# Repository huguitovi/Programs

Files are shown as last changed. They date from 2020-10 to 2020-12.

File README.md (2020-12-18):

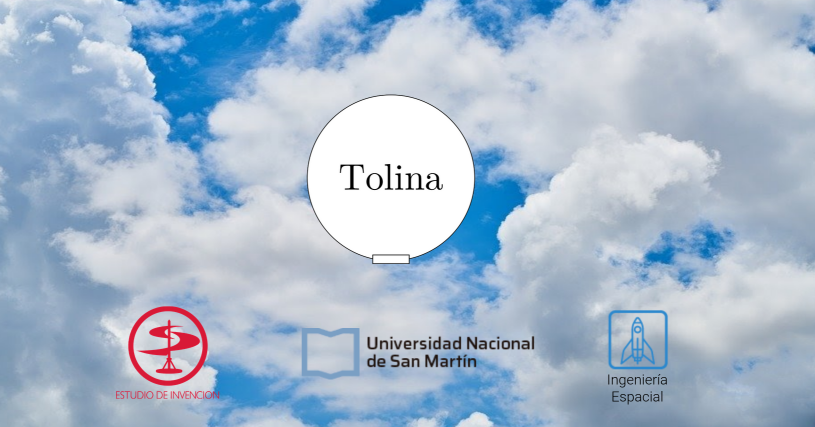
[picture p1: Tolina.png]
GitHub Logo


## Sobre Tolina

Tolina es un dirigible esférico, proyecto perteneciente a los estudiantes del segundo cuatrimestre de 2020 de la materia Proyecto Integrador II, de la carrera de [Ingenieria Espacial](http://www.unsam.edu.ar/ingenierias/#ingenierias) perteneciente a
la [Escuela de Ciencia y Tecnología](http://www.unsam.edu.ar/escuelas/ciencia/) de la [UNSAM](https://www.unsam.edu.ar/).

## Ingeniería Espacial
Argentina es uno de los siete países que tienen satélites propios. Los proyectos para aumentar la soberanía espacial demandan ingenieros con esta formación. Podrás diseñar vehículos y dispositivos cuyo ambiente está en el espacio, donde hay vacío, radiaciones electromagnéticas, temperaturas bajo cero y meteoritos. Esta es la primera carrera de América Latina en su tipo y tiene una orientación en sistemas complejos. La creatividad, la inventiva y la innovación son las habilidades esenciales de cualquier ingeniero. La Ingeniería Espacial implementará una nueva pedagogía para concebir, diseñar, implementar y operar sistemas, productos y servicios espaciales. Los alumnos participarán de proyectos integradores y multidisciplinarios dentro de un [Estudio de Invención](http://estudiodeinvencion.com.ar), que contará con un laboratorio de prototipado rápido y amplios espacios de trabajo con todas las herramientas y técnicas digitales modernas.

## Audiencia. ¿Para quién está pensado?
Tolina es realizado en medio de una crisis de salud mundial generada por la Pandemia de COVI-19, de tal forma es pensado como un medio para permitir a sus usarios una forma alternativa, de largo alcance de radiofrecuencia, larga vida de las baterias, para gestionar la logistica prioritaria de las vacunas a sectores de dificil acceso, tanto como de distintas mercancias, salvaguardando la salud y manteniendo la distncia social, recomendada por la [OMS](https://www.aaoms.org/practice-resources/covid-19-updates).

## Contenido
El objetivo de este repositorio es permitir al equipo trabajar desde sus casas, mantener al día los cambios de versión, abrir el trabajo a la comunidad y de esta forma gestionar más eficientemente el tiempo de desarrollo y ensayos de los distintos subsistemas.

## Requerimientos
Para utilizar estos códigos es necesario tener un PCDuino4 nano, el kit de desarrollo LoRaWAN ofrecido por Elemon SAMR34, clon de [Penguino Feather SAMR34](https://makertronika.com/penguino-samr34/) y demas componentes detallados en el [BOM](https://docs.google.com/spreadsheets/d/1q8VCjkfIKXkzYkmn2R5FzP_4t8kTszAMtYl-jQM-gV4/edit?usp=sharing). Los requermientos de sistema se detallan [aquí](https://github.com/huguitovi/Tolina/blob/master/documentos/Requerimientos.md).

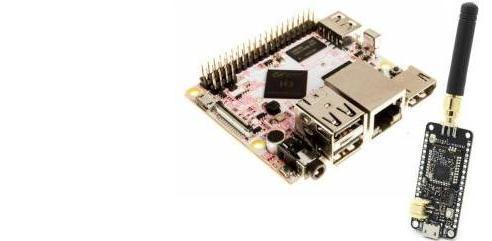
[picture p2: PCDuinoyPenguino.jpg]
image info


## Dedicación y duración
Este proyecto dura un cuatrimestre y es de dedicación completa por parte del equipo de estudiantes que en este tiempo deben tener listo y operativo el dirigible.

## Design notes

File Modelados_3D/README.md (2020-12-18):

# Modelados 3D

Tanto como para la determinación del centro de masa, como para facilitar aspectos relacionados a la integración realizada a distancia y en forma descentralizada, se realizaron los siguientes modelados 3D:

## PCDuino4 nano

Fabricante: [LinkSprite](https://www.linksprite.com/pcduino4-nano/)
Modelado: [OnShape](https://cad.onshape.com/documents/b4b0b3f34a575819a2707872/w/88d6b2fa41ddc3f8a9d6b3d2/e/b33581a21ca1b7f09e8596de)

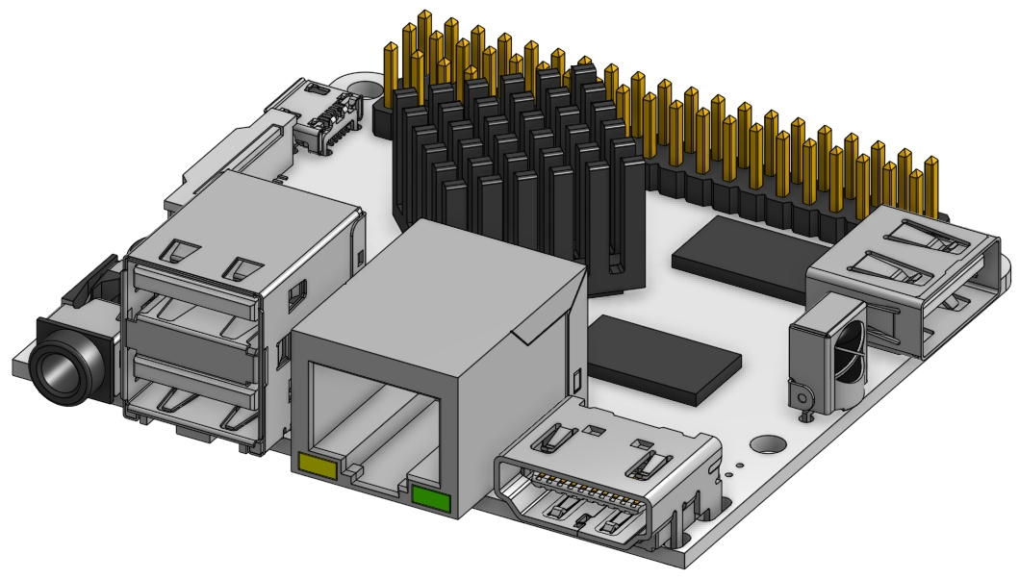
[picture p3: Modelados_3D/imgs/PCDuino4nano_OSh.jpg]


## EESAM34R

Fabricante: [Elemon](https://www.elemon.com.ar/Cotizar.aspx)
Modelado: [OnShape](https://cad.onshape.com/documents/ec4b6312847b79863e13bf8e/w/0436242ac0876fc591eb0102/e/217696dc8bc2e912b344ecc6)

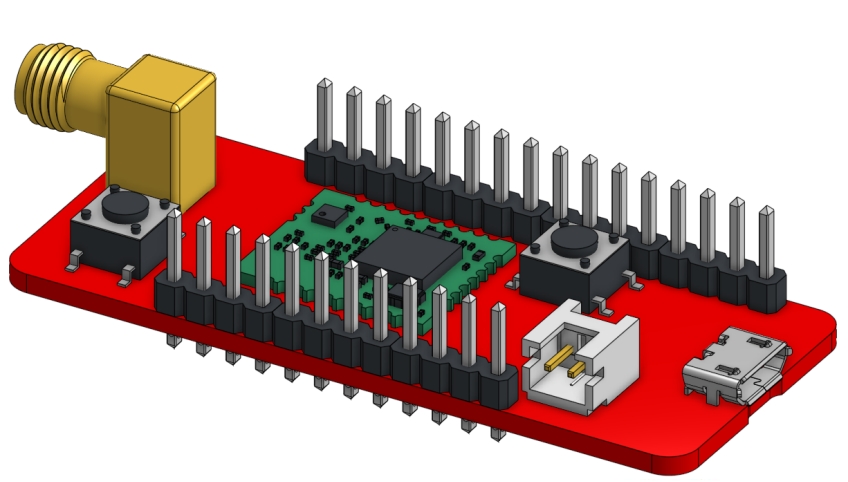
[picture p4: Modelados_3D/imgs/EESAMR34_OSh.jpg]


## Antena SGSM008-SMA/M-R/A-5

Fabricante: [Elemon](https://www.elemon.com.ar/Cotizar.aspx)
Modelado: [OnShape](https://cad.onshape.com/documents/461af691bdc8e8293b6acc81/w/5bf0a661077147eb908c0616/e/5cb2624135b9eea222923b98)

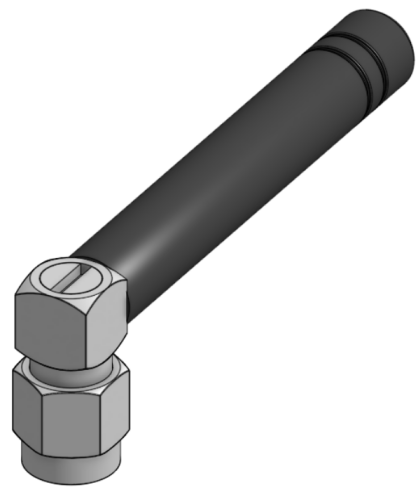
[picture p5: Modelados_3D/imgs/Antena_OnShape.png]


## PCB dedicado (Modulo controlador de 8 motores nativo de Tolina)

Fabricante: [Tolina](https://github.com/huguitovi/Tolina)
Modelado: [OnShape](https://cad.onshape.com/documents/81b609bb43d320c6a6baf298/w/e704fe0701eedfa0513e0479/e/23b6f936ed0f58f585dd623b)

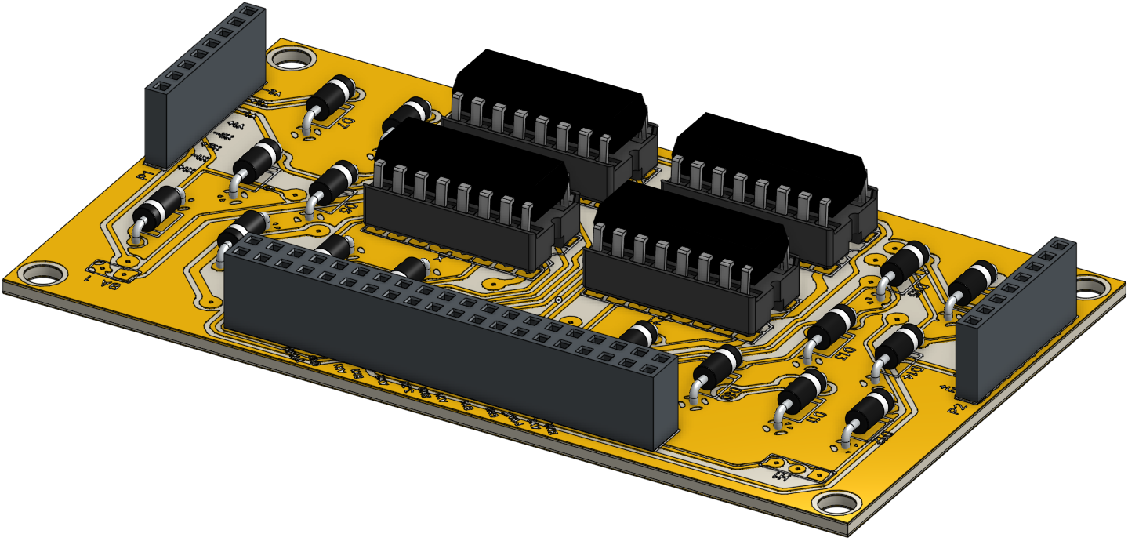
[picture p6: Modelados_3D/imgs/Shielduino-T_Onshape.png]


## Logitech C200 WebCam desarmada

Fabricante: [Logitech](https://support.logi.com/hc/en-us/articles/360023307014-Logitech-Webcam-C200-Technical-Specifications)
Modelado: [OnShape](https://cad.onshape.com/documents/c44ed40a48549f56abfa6e95/w/bb11458fc9d157a45261392b/e/d3aeba1b3881ed7b99e6e940)

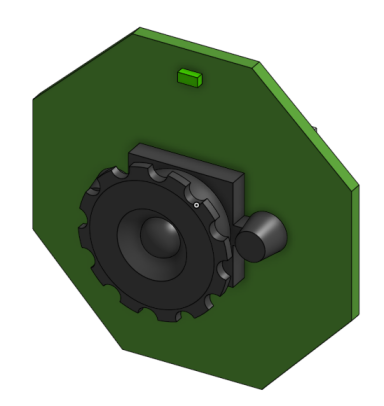
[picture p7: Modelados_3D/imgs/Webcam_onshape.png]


## SRF04

Modelado: [OnShape](https://cad.onshape.com/documents/197cf291449f2230b7baf36f/w/e24e00b610793ed7f297869d/e/b949f0ee36fcf4b4ce4800be)

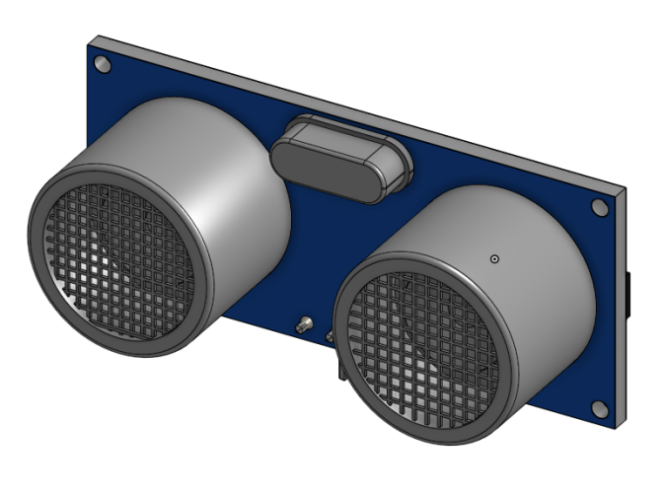
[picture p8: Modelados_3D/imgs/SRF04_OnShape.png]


## MPU9250 BMP260

Fabricante: [Bosch](https://www.bosch.com/)
Modelado: [OnShape](https://cad.onshape.com/documents/137634499555791615642d57/w/9201c79dbb14d58388e90772/e/1ceaf7b055e3bd4cd616bf7e)

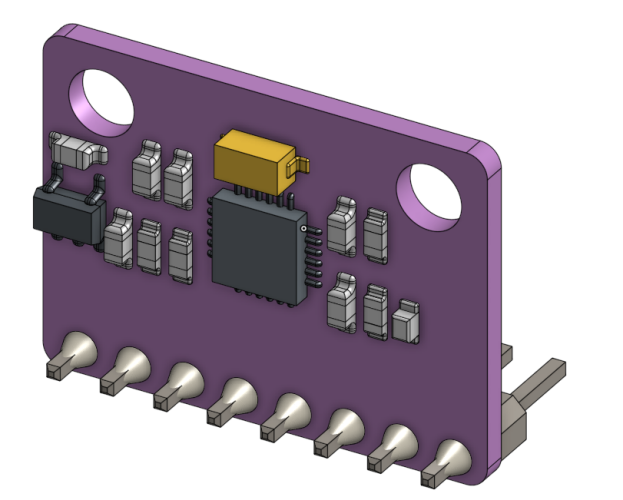
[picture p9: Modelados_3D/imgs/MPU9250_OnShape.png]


## JSN-SR04T

Fabricante: [JSN](https://www.elemon.com.ar/Cotizar.aspx)
Modelado: [OnShape](https://cad.onshape.com/documents/5689bac8cee0096f19e13d54/w/39e027f5c27cfc006658e57e/e/44e5082090eb61c592169ccd)

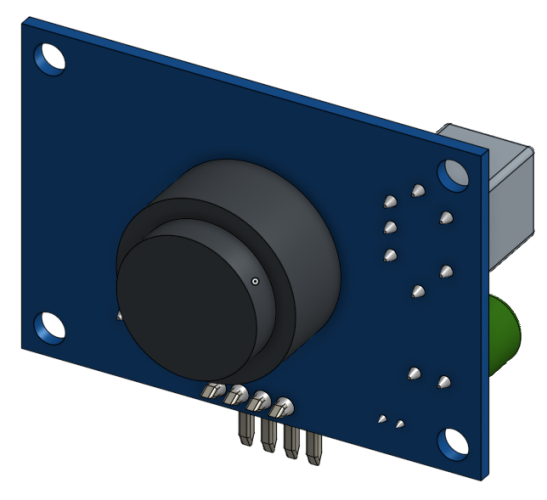
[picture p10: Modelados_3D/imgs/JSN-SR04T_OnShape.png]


## EESAM34R

Fabricante: [I-O Data]()
Modelado: [OnShape](https://cad.onshape.com/documents/2a58d5fc7cfdaa5131b7bced/w/1790b3b75a4a6e0e9be4c743/e/e5ab12a85833402ce6b296c1)

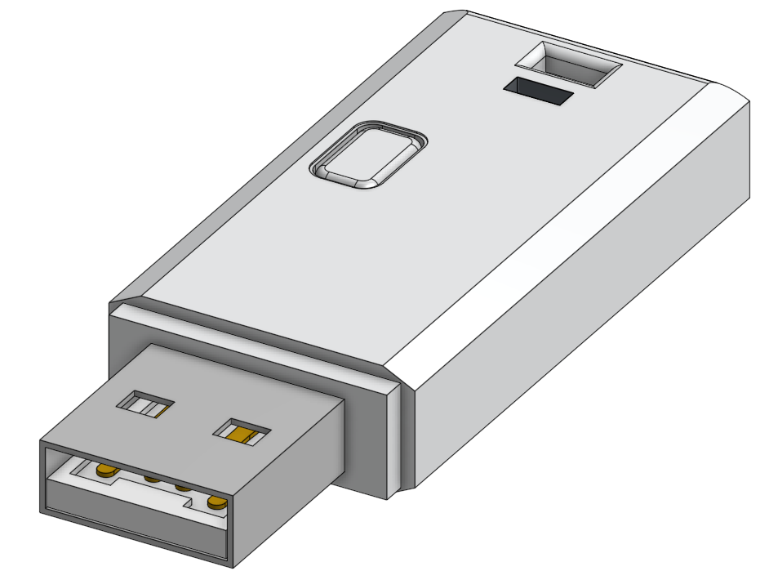
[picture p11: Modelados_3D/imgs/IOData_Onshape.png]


## Arduino nano

Fabricante: [Arduino CC](https://www.arduino.cc/)
Modelado: [OnShape](https://cad.onshape.com/documents/e08e87ede2b085dabb8ec284/w/2d2faaebe3f86c9a17560737/e/5b4681878ee84e214a5b4865)

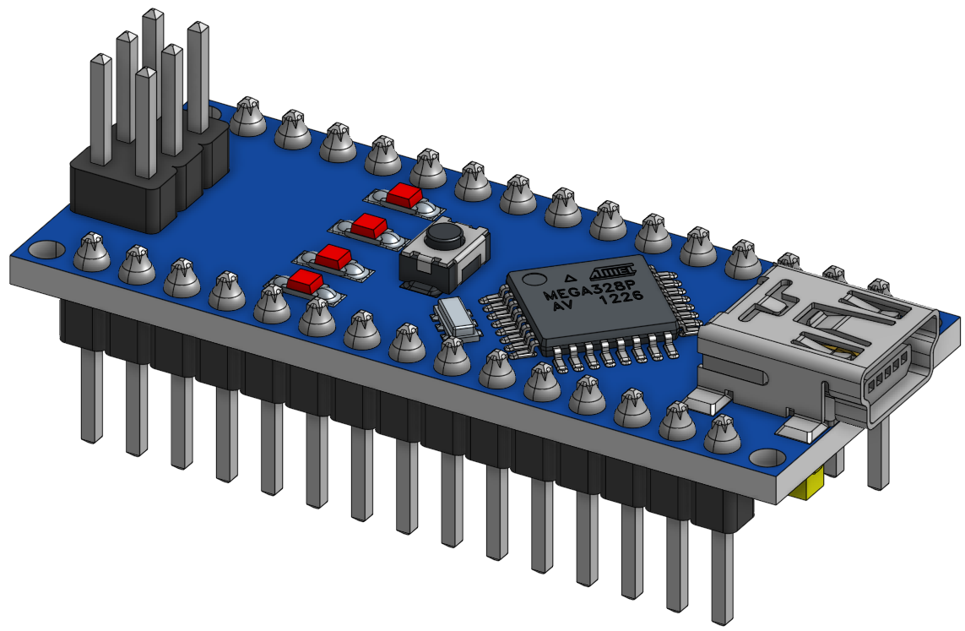
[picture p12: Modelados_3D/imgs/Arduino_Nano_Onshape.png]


## Shield Motores Arduino

Fabricante: [Adafruit/LadyAda](https://www.adafruit.com/product/81)
Modelado: [OnShape](https://cad.onshape.com/documents/8d47852de01c4f7387d6f724/w/a000db7d16f8f21633216dc9/e/aa8d04f9ba54ca66b5974670)

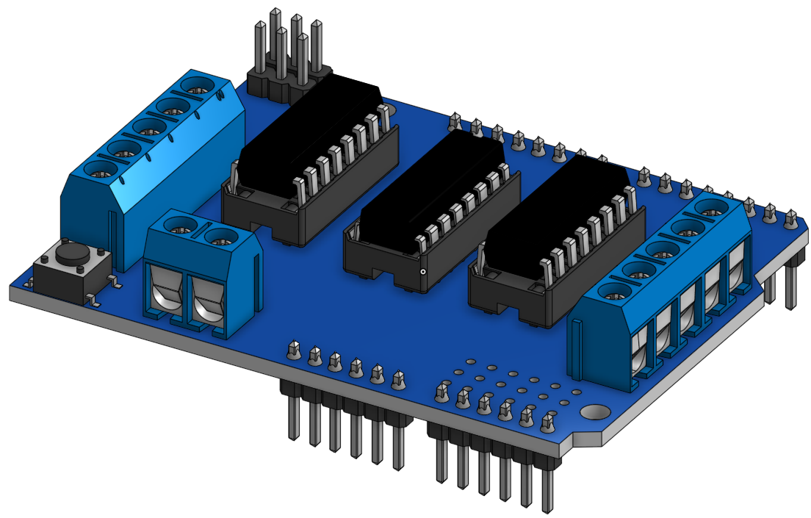
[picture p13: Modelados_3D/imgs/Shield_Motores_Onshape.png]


## Motor con reductor y helice (Gear Box 820 Coreless Cw Motor + Propeller Combo Set)

Fabricante: [Gear Box 820 Coreless Cw Motor + Propeller Combo Set](https://www.adafruit.com/product/81)
Modelado: [OnShape](https://cad.onshape.com/documents/0da1457debc2a4a932a4e4b8/w/93f8d65b40d40a5ed462e47c/e/6945122e04e86da24dd1f20e)

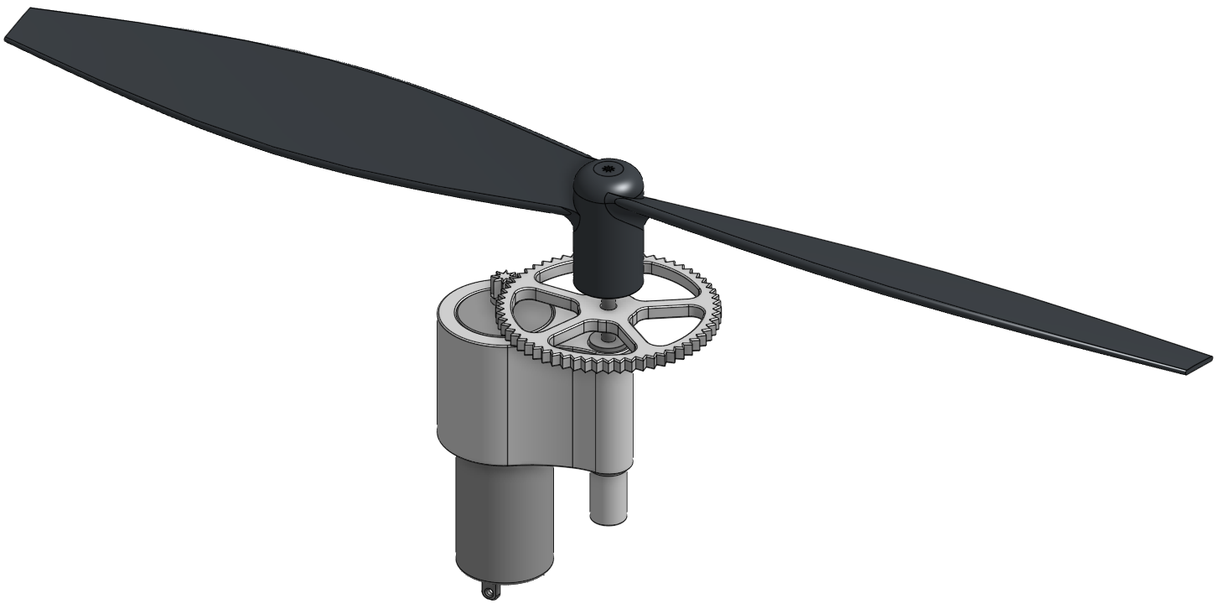
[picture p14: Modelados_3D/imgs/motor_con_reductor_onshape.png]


## Palanca de comando (KY-023 Dual Axis Joystick Module)

Fabricante: [KY-023](https://arduinomodules.info/ky-023-joystick-dual-axis-module/)
Modelado: [OnShape](https://cad.onshape.com/documents/0726fa1b1b917e7525642e5a/w/507874bc5735f5b12601344c/e/7aaea927ce7cc22c705d6ab0)

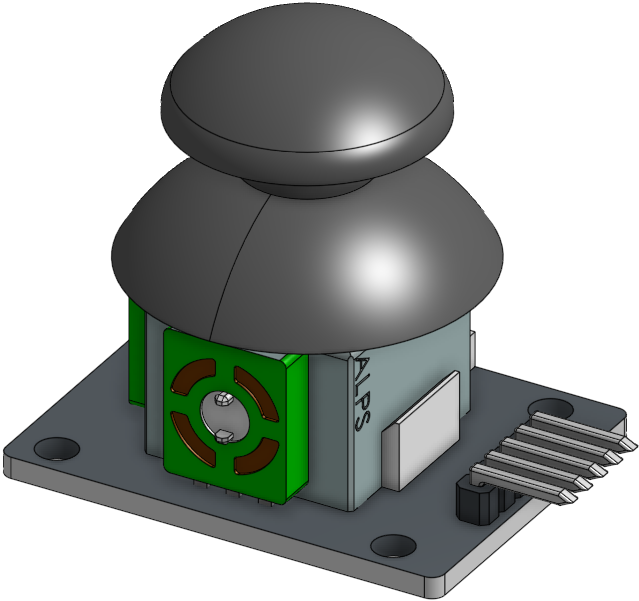
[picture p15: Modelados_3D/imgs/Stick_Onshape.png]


## Power Bank, Banco de baterias de celular.

Modelado: [OnShape](https://cad.onshape.com/documents/737381daf216fbd5854f3add/w/87e22c1f60c919123eda144f/e/50bee117e4f35970c11e8889)

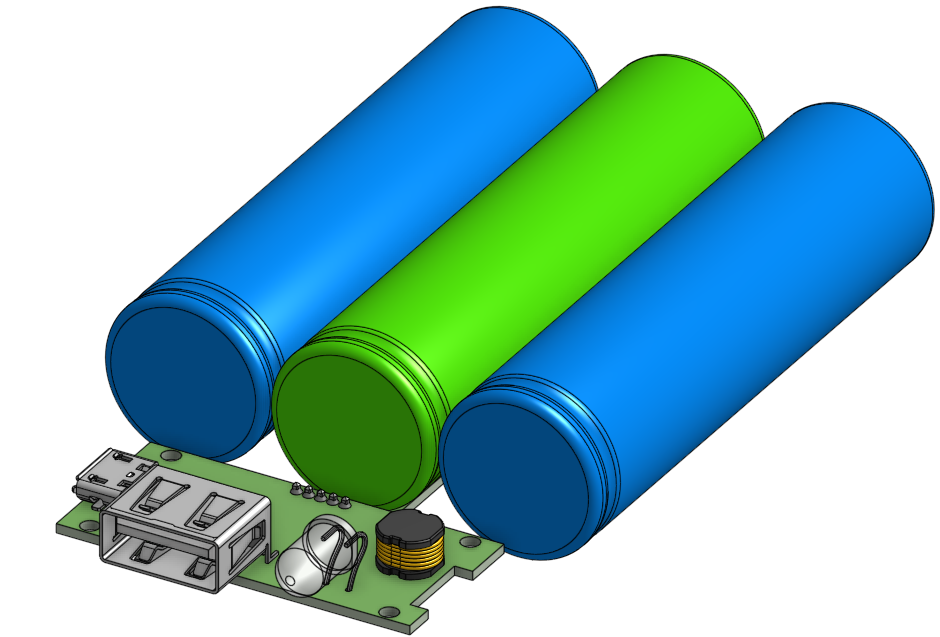
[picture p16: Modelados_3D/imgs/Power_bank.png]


## RF433 Receptor y transmisor

#### Emisor
Modelado: [OnShape](https://cad.onshape.com/documents/c004816032ad218b156599f2/w/bebf56a0e8003108964e5747/e/70b6ae09fcd66aa26aaf5e35)

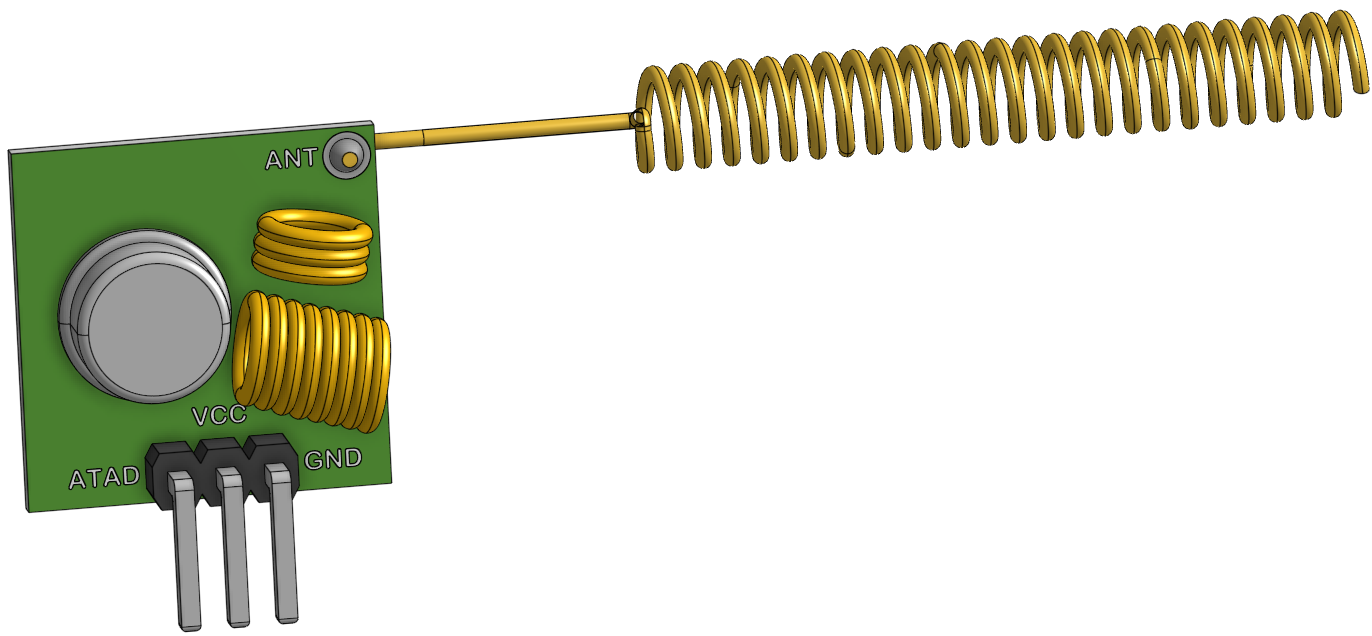
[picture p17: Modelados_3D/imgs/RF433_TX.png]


#### Receptor
Modelado: [OnShape](https://cad.onshape.com/documents/db5adeeefbcc91026425b5d4/w/9b04f95ce5a829f2a64d8bc5/e/4a731cc7295ea3d0d6fe656e)

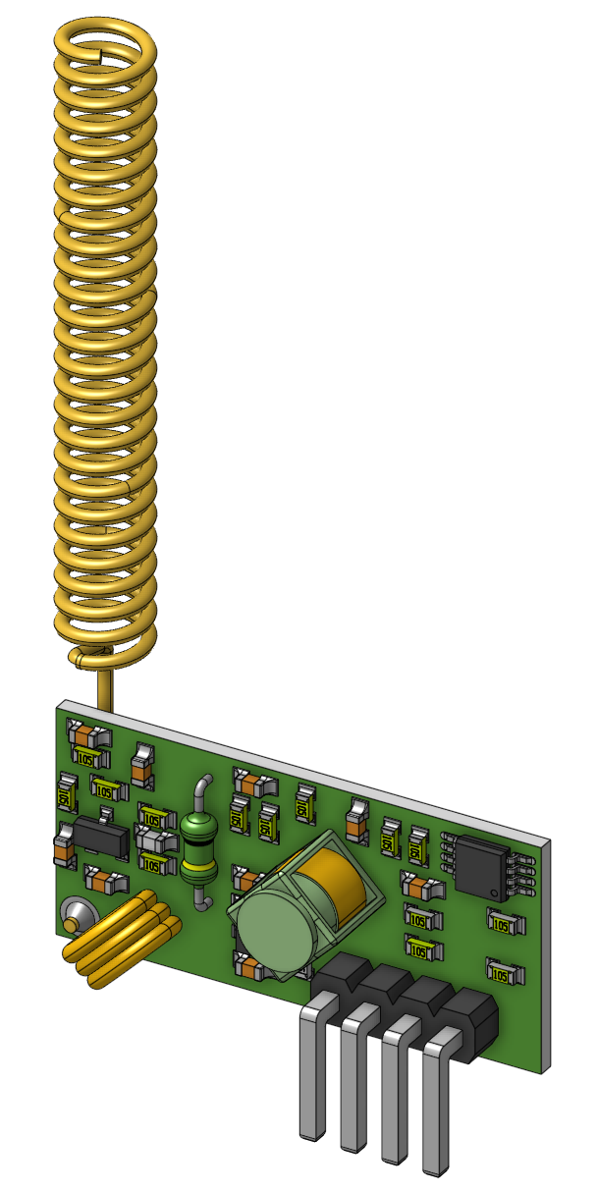
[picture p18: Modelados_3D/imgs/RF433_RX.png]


## Vistas explotadas de Comando y Carga útil

#### Comando
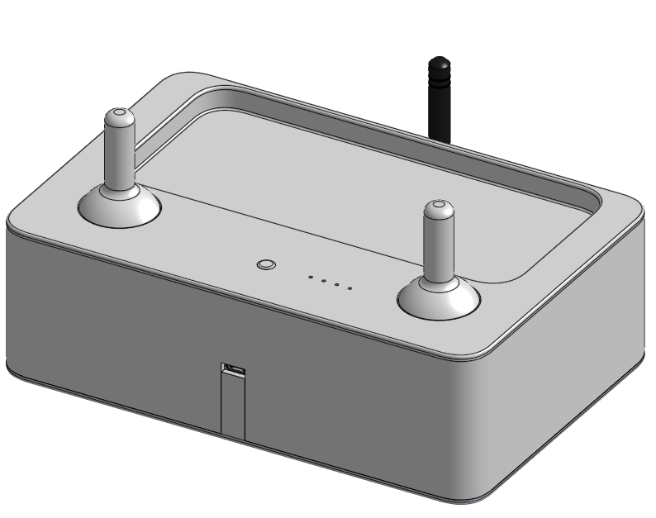
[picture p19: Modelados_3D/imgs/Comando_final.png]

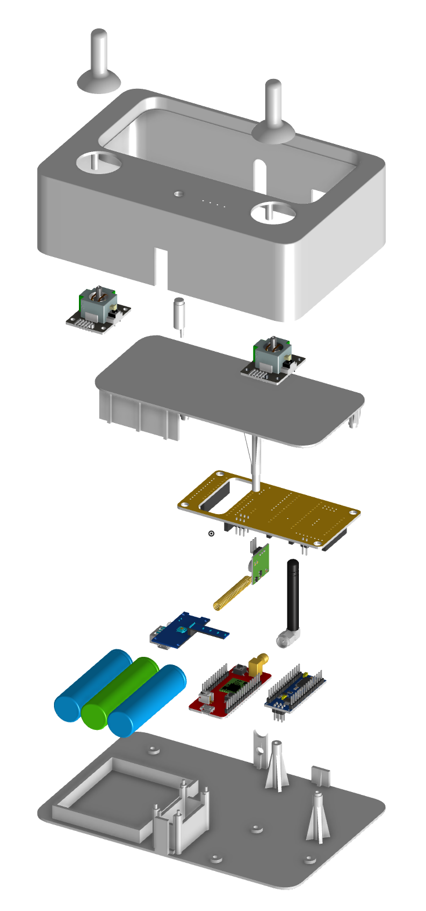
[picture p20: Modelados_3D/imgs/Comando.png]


#### Carga útil
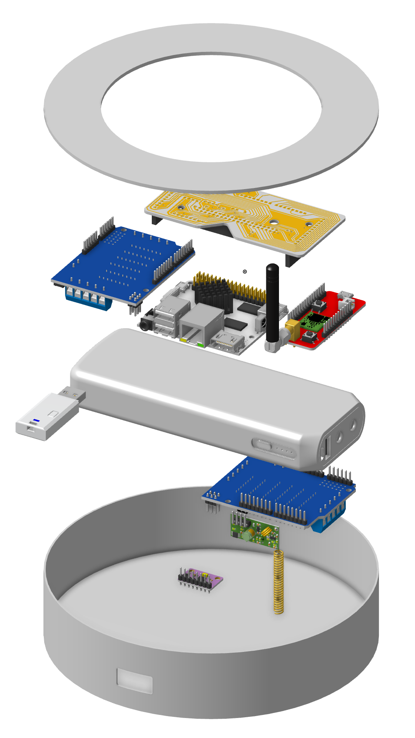
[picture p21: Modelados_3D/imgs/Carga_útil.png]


###### PCB de interconexion en Carga útil
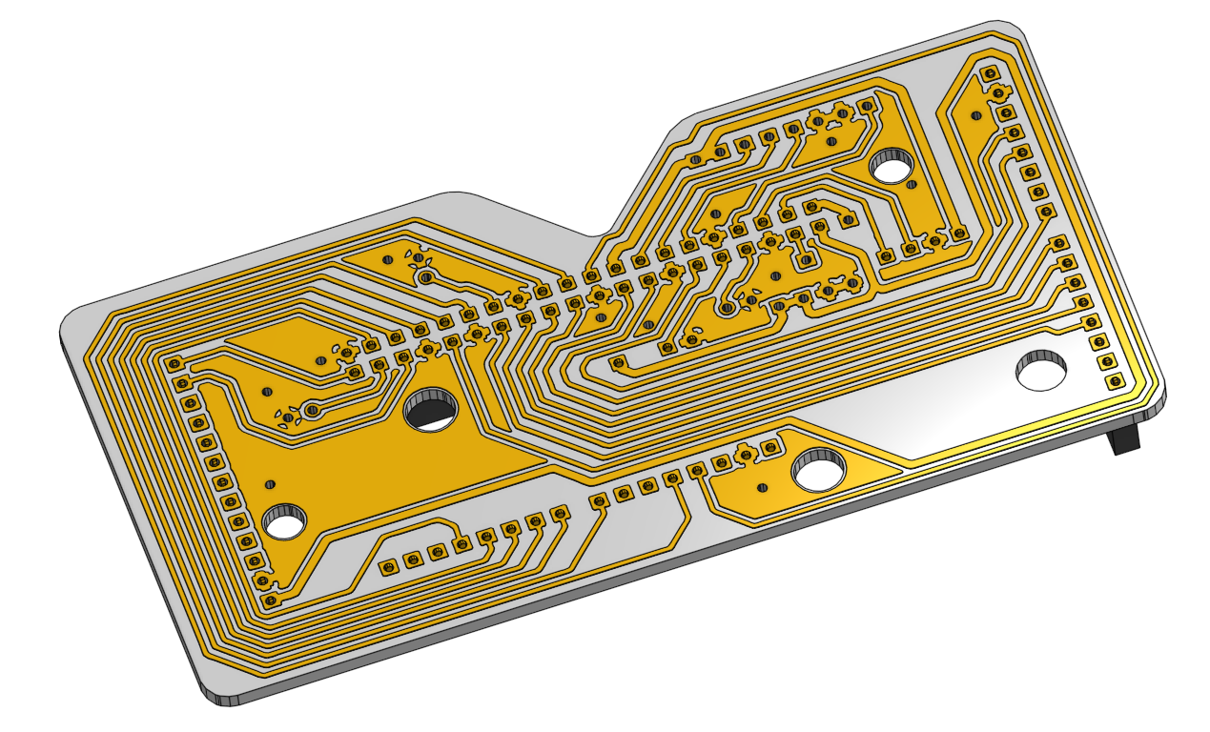
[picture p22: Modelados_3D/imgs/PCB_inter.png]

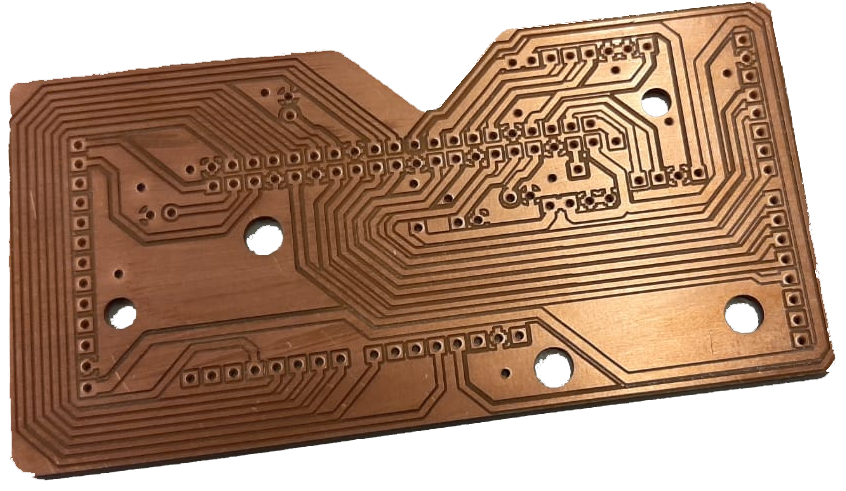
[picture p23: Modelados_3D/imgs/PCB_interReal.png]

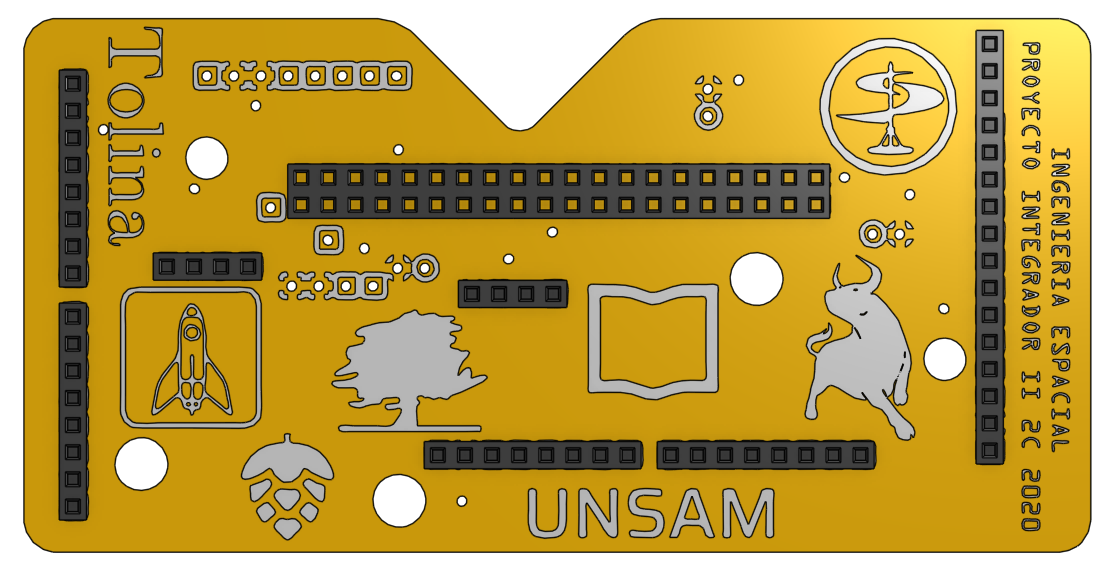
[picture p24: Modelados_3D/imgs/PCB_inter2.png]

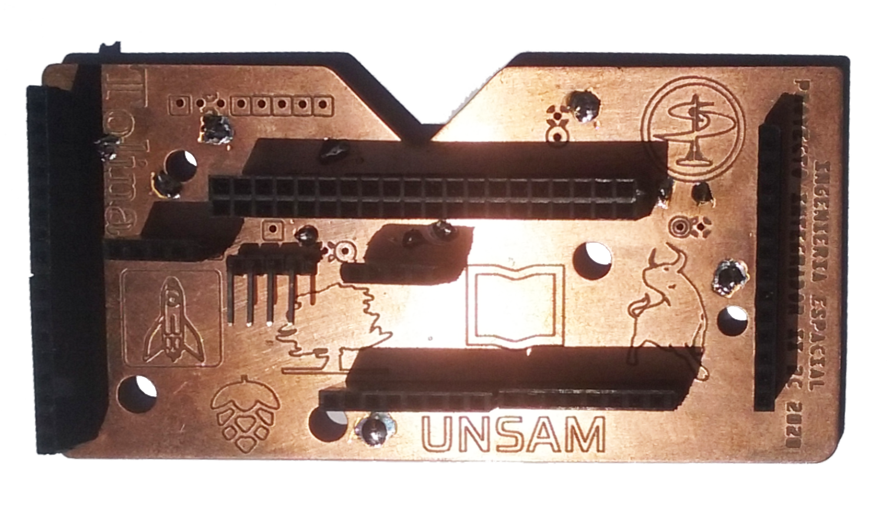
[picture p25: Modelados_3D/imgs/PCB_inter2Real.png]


<!---just---#

![image info](./imgs/SRF04_OnShape.png)
![image info](./imgs/MPU9250_OnShape.png)
![image info](./imgs/JSN-SR04T_OnShape.png)>

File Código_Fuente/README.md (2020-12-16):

## Sobre Código Fuente

En esta carpeta se encuentran las fuentes en desarrollo y librerias base utilizadas para darle vida a Tolina, en su totalidad son desarrollos en Lenguaje C.

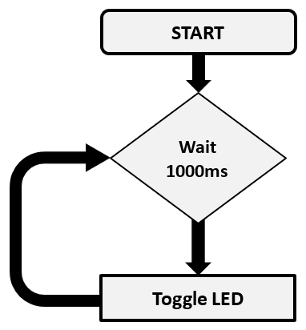
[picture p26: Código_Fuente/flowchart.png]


### Diagrama de software del Comando

image info

### Diagrama de software de Comunicación

image info

### Diagrama de software de Carga Útil

image info
image info

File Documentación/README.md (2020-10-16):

## Requerimientos del Modelo de Ingeniería

1. Nomenclatura de Requerimientos
2. Requerimientos de Misión (MIS)
3. Requerimientos de Sistema (SIS) - Preliminar
4. Requerimientos de Carga Útil (PAY) - Preliminar
5. Requerimientos de Estructura (STR) - Preliminar
6. Requerimientos de Comunicaciones (COM) - Preliminar
7. Requerimientos de Comando y manejo de datos (C&DH) - Preliminar
8. Requerimientos de Potencia (POT) - Preliminar
9. Requerimientos de Propulsión (PRO) - Preliminar
10. Requerimientos de Guiado, Navegación y Control (GN&C) - Preliminar
11. Requerimientos de Estación Terrena (GST) - Preliminar

## 1. Nomenclatura de Requerimientos:

Los requerimientos de este documento siguen una nomenclatura según normativa del estándar ESA aeroespacial del tipo:

X-XXX-NNN

Donde el primer carácter es el prefijo que denota el tipo de requerimiento; los tres caracteres siguientes son el código de la categoría a la que pertenece el requerimiento (por ejemplo, el subsistema al que aplica y los últimos tres caracteres son el código numérico del requerimiento.

Los tipos de requerimientos son:

De diseño, denotados por una letra D.

Funcionales, denotados por una letra F.

De performance, denotados por una letra P.

Restrictivos, denotados por una letra R.

## 2. Requerimientos de Misión (MIS)
**F-MIS-010**	Se deberá concebir, diseñar, implementar y operar, el sistema completo, de un modelo de ingeniería, capaz de ensayar en tierra, capacidades específicas del dirigible propuesto en el proyecto Tolina.

## 3. Requerimientos de Sistema (SIS) - Preliminar
**P-SIS-010**	El dirigible Tolina deberá tener un radio de operación de al menos 30 m desde la GST.

**F-SIS-011**	El dirigible Tolina deberá brindar tres grados de libertad de traslación en el espacio de forma controlada.

**F-SIS-012**	El dirigible deberá brindar el grado de rotación de yaw de forma controlada.

**F-SIS-013**	El dirigible deberá presentar equilibrio mecánico estable en su rotación en torno a los ejes de roll y pitch a lo largo de toda la misión.

**F-SIS-020**	Los datos e imágenes obtenidos por la Tolina deberán ser transmitidos inalámbricamente hacia la estación terrena.

**F-SIS-030**	El dirigible deberá tener comunicación permanente con la estación terrena.

**P-SIS-040**	El dirigible deberá poder ser operado hasta por lo menos 3 m de altura.

**P-SIS-050**	El dirigible deberá tener una autonomía de por lo menos 30 minutos.

**R-SIS-060**	El volumen de helio contenido en módulo de flotación deberá ser inferior a 1.5 m3.

**R-SIS-061**	El dirigible deberá tener una masa total inferior a 1,5 kg.

**R-SIS-070**	El proyecto completo deberá consistir de un costo inferior a $30000.

**P-SIS-080**	El subsistema de potencia deberá proveer energía al Sistema al menos durante 30 minutos.

## 4. Requerimientos de Carga Útil (PAY) - Preliminar

**D-PAY-010**	El dirigible deberá contar con una cámara para capturar imágenes.

**D-PAY-011**	La cámara fotográfica deberá apuntar hacia nadir con una tolerancia de 10°.

**P-PAY-012**	La cámara fotográfica deberá proporcionar una pisada de por lo menos 2 m.

**P-PAY-013**	La cámara fotográfica deberá contar con una resolución de por lo menos 1 cm/px.

**R-PAY-020**	La carga útil de la Tolina deberá tener una masa inferior a TBD kg.

**R-PAY-030**	La carga útil de la Tolina deberá tener un consumo operativo menor a TBD mAh (crecimiento: 40%).

## 5. Requerimientos de Estructura (STR) - Preliminar

**D-STR-010**	El dirigible deberá consistir de dos módulos: un módulo de flotación y un módulo instrumental.

**F-STR-020**	El módulo de flotación deberá proveer al Tolina de flotación entre -TBD N y 0 N a lo largo de toda la misión.

**R-STR-021**	El gas helio en el módulo de flotación deberá estar a una presión absoluta de entre 1 atm y 1,1 atm a lo largo de toda la misión.

**D-STR-022**	La forma del módulo de flotación deberá optimizar la relación Volumen/Superficie.

**F-STR-030**	El módulo instrumental deberá alojar a la carga útil, y permitir que esta cumpla con todos los requerimientos definidos en la Sección 4.

**F-STR-031**	El módulo instrumental deberá alojar al subsistema de comunicaciones, y permitir que este cumpla con todos los requerimientos definidos en la Sección 6.

**F-STR-032**	El módulo instrumental deberá alojar al subsistema de C&DH, y permitir que este cumpla con todos los requerimientos definidos en la Sección 7.

**F-STR-033**	El módulo instrumental deberá alojar al subsistema de potencia, y permitir que este cumpla con todos los requerimientos definidos en la Sección 8.

**F-STR-034**	El módulo instrumental deberá alojar al subsistema de GN&C, y permitir que este cumpla con todos los requerimientos definidos en la Sección 10.

**D-STR-040**	El módulo instrumental deberá estar adherido a la parte inferior del módulo de flotación a lo largo de toda la misión.

## 6. Requerimientos de Comunicaciones (COM) - Preliminar

**F-COM-010**	El subsistema de comunicaciones deberá proveer comunicaciones en ambos sentidos para el subsistema GST.

**F-COM-011**	El subsistema de comunicaciones deberá contar con la capacidad de comunicarse con GST a un nivel de mínimo de TBD dB en cualquier configuración de actitud.

**F-COM-012**	El subsistema de comunicaciones deberá ser capaz de recibir comandos desde GST en cualquier momento de su misión.

**F-COM-013**	El subsistema de comunicaciones deberá ser capaz de transmitir todos los datos científicos a la GST.

**F-COM-014**	El subsistema de comunicaciones deberá ser capaz de transmitir todos los datos de ingeniería a la GST.

**F-COM-020**	El subsistema de comunicaciones deberá proveer comunicaciones en sentido de recepción para el subsistema PRO.

**F-COM-021**	El subsistema de comunicaciones de PRO deberá ser capaz de recibir comandos desde GST en cualquier momento de su misión.

**F-COM-030**	El subsistema de comunicaciones deberá proveer comunicaciones en sentido de emisión para el subsistema PAY.

**F-COM-031**	El subsistema de comunicaciones de PAY deberá ser capaz de enviar datos hacia GST en todo momento de su misión.

**P-COM-032**	La comunicación de PAY con GST deberá permitir el flujo de datos correspondiente al envío de imágenes de resolución mínima 320x240px.

**F-COM-040**	El subsistema de comunicaciones deberá proveer comunicaciones en sentido de emisión para el subsistema GN&C.

**F-COM-041**	El subsistema de comunicaciones de GN&C deberá ser capaz de enviar datos hacia GST en cualquier momento de su misión.

**P-COM-050**	El subsistema de comunicaciones deberá operar con una latencia menor a TBD ms.

## 7. Requerimientos de Comando y manejo de datos (C&DH) - Preliminar

**F-CDH-010**	El subsistema deberá soportar un sistema operativo en tiempo real.

**F-CDH-020**	El subsistema deberá proveer capacidad de procesamiento de datos.

**F-CDH-030**	El subsistema deberá asegurar transferencia de datos entre subsistemas.

**F-CDH-040**	El subsistema deberá asegurar transferencia de comandos entre subsistemas.

**F-CDH-050**	El subsistema deberá generar flujo de telemetría.

## 8. Requerimientos de Potencia (POT) - Preliminar

**R-POT-010**	El dirigible deberá tener un consumo operativo total menor a 10000 mAh.

**D-POT-011**	El dirigible deberá poseer una celda de potencia exclusiva para OBC y payload, llamada BATERÍA1.

**D-POT-012**	El dirigible deberá poseer una celda de potencia exclusiva para Propulsión, llamada BATERÍA2.

**P-POT-020**	La BATERÍA1 de potencia deberá alimentar a la OBC durante por lo menos 30 minutos de operación.

**P-POT-021**	La OBC deberá alimentar al payload durante por lo menos 30 minutos de operación.

**P-POT-030**	La BATERÍA2 de potencia deberá alimentar a los motores durante por lo menos 30 minutos de operación.

**R-POT-040** 	La BATERIA2 deberá tener un C-Rate mayor a 4C.

**D-POT-050** 	La BATERIA2 deberá ser de li-po o li-ion de 1 o 2 celdas. (TBC)

**R-POT-060** 	La celda de potencia deberá pesar menos de 400 g. (TBC)

**D-POT-070**	Las dimensiones de las baterías no deberán superar a las dimensiones internas de la góndola (TBC).

**F-POT-080**	Las baterías deberán ser recargables (reutilizables).

**R-POT-090**	Los motores de Tolina deberán poder operar en un rango nominal de voltajes entre 3.7 V y 7.4 V.

**R-POT-091**	Cada motor de Tolina deberá tener un consumo operativo menor a 1500 mAh.

## 9. Requerimientos de Propulsión (PRO) - Preliminar

**P-PRO-010**	Cada motor de Tolina deberá proporcionar un empuje de al menos 20 gf (TBC).

**F-PRO-011**	Cada motor deberá proporcionar empuje variable.

**D-PRO-020**	Cada motor deberá estar alojado en un soporte removible.

**R-PRO-030**	Los motores deberán pesar menos de 20 g cada uno (TBC).

**F-PRO-040**	Los motores deberán ser dispuestos de manera que aporten al vehículo los grados de libertad mencionados en F-SIS-011 y F-SIS-012.

**F-PRO-050**	Cada motor deberá poder girar en ambos sentidos.

## 10. Requerimientos de Guiado, Navegación y Control (GN&C) - Preliminar

**F-GNC-010**	El dirigible deberá sensar la magnitud y componentes de aceleración lineal con un error admisible de TBD m/s2 a lo largo de toda la misión.

**F-GNC-020**	El dirigible deberá medir su distancia al suelo a lo largo de toda la misión.

## 11. Requerimientos de Estación Terrena (GST) - Preliminar

**P-GST-010**	La Estación Terrena deberá recibir señal de video con una latencia de hasta TBD ms.

**F-GST-020**	La Estación Terrena deberá recibir telemetría del dirigible.

**P-GST-021**	La Estación Terrena deberá comunicarse con el dirigible durante al menos 30  min.

**F-GST-030**	La Estación Terrena deberá incluir soporte para visualización de las imágenes captadas por la cámara.

**P-GST-040**	La Estación Terrena deberá contar con capacidad de almacenamiento de los datos de por lo menos 8 GB.

**F-GST-050**	La Estación Terrena deberá permitir operar manualmente el dirigible.

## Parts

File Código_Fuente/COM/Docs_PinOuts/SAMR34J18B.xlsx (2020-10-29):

SAM R34/R35 Pin | I/O Pin | Supply | A |  | B(1)(2) |  |  |  |  | C | D | E | F | G | H | I
 |  |  | EIC | RSTC | REF | ADC | AC | PTC X-lines | PTC Y- | SERCOM (1)(2) | SERCOM- ALT | TC/TCC | TCC | COM | AC/GCLK/SUPC | CCL
A3 | PA00 | VSWOUT | EXTINT[0] | EXTWAKE[0] | — | — | — | — | lines | — | SERCOM1/PAD[0] | TCC2/WO[0] | — | — | — | —
A4 | PA01 | VSWOUT | EXTINT[1] | EXTWAKE[1] | — | — | — | — | — | — | SERCOM1/PAD[1] | TCC2/WO[1] | — | — | — | —
D3 | PA04 | VDDANA | EXTINT[4] | EXTWAKE[4] | VREFB | AIN[4] | AIN[0] | — | — | — | SERCOM0/PAD[0] | TCC0/WO[0] | — | — | — | CCL0/ IN[0]
C4 | PA05 | VDDANA | EXTINT[5] | EXTWAKE[5] | — | AIN[5] | AIN[1] | — | — | — | SERCOM0/PAD[1] | TCC0/WO[1] | — | — | — | CCL0/ IN[1]
E3 | PA06 | VDDANA | EXTINT[6] | EXTWAKE[6] | — | AIN[6] | AIN[2] | — | — | — | SERCOM0/PAD[2] | TCC1/WO[0] | — | — | — | CCL0/ IN[2]
F3 | PA07 | VDDANA | EXTINT[7] | EXTWAKE[7] | — | AIN[7] | AIN[3] | — | Y[4] | — | SERCOM0/PAD[3] | TCC1/WO[1] | — | — | — | CCL0/OUT[0]
F4 | PA08 | VDDIO | NMI | — | — | AIN[16] | — | X[0] | — | SERCOM0/PAD[0] | SERCOM2/PAD[0] | TCC0/WO[0] | TCC1/WO[2] | — | — | CCL1/ IN[3]
F5 | PA09 | VDDIO | EXTINT[9] | — | — | AIN[17] | — | X[1] | Y[6] | SERCOM0/PAD[1] | SERCOM2/PAD[1] | TCC0/WO[1] | TCC1/WO[3] | — | — | CCL1/ IN[1]
F6 | PA13 | VDDIO | EXTINT[13] | — | — | — | — | — | Y[7] | SERCOM2/PAD[1] | SERCOM4/PAD[1] | TCC2/WO[1] | TCC0/WO[7] | — | AC/CMP[1] | —
F8 | PA14 | VDDIO | EXTINT[14] | — | — | — | — | — | — | SERCOM2/PAD[2] | SERCOM4/PAD[2] | TC4/ WO[0] | TCC0/WO[4] | — | GCLK_IO[0] | —
G8 | PA15 | VDDIO | EXTINT[15] | — | — | — | — | — | — | SERCOM2/PAD[3] | SERCOM4/PAD[3] | TC4/ WO[1] | TCC0/WO[5] | — | GCLK_IO[1] | —
F7 | PA16 | VDDIO | EXTINT[0] | — | — | — | — | X[4] | — | SERCOM1/PAD[0] | SERCOM3/PAD[0] | TCC2/WO[0] | TCC0/WO[6] | — | GCLK_IO[2] | CCL0/ IN[0]
E6 | PA17 | VDDIO | EXTINT[1] | — | — | — | — | X[5] | — | SERCOM1/PAD[1] | SERCOM3/PAD[1] | TCC2/WO[1] | TCC0/WO[1] | — | GCLK_IO[3] | CCL0/ IN[1]
E7 | PA18 | VDDIO | EXTINT[2] | — | — | — | — | X[6] | — | SERCOM1/PAD[2] | SERCOM3/PAD[2] | TC4/ WO[0] | TCC0/WO[2] | — | AC/CMP[0] | CCL0/ IN[2]
E8 | PA19 | VDDIO | EXTINT[3] | — | — | — | — | X[7] | — | SERCOM1/PAD[3] | SERCOM3/PAD[3] | TC4/ WO[1] | TCC0/WO[3] | — | AC/CMP[1] | CCL0/OUT[0]
D8 | PA22 | VDDIO | EXTINT[6] | — | — | — | — | X[10] | — | SERCOM3/PAD[0] | SERCOM5/PAD[0] | TC0/ WO[0] | TCC0/WO[4] | — | GCLK_IO[6] | CCL2/ IN[0]
D7 | PA23 | VDDIO | EXTINT[7] | — | — | — | — | X[11] | — | SERCOM3/PAD[1] | SERCOM5/PAD[1] | TC0/ WO[1] | TCC0/WO[5] | USB/SOF 1 kHz[6] | GCLK_IO[7] | CCL2/ IN[1]
B8 | PA24 | VDDIO | EXTINT[12] | — | — | — | — | — | — | SERCOM3/PAD[2] | SERCOM5/PAD[2] | TC1/ WO[0] | TCC1/WO[2] | USB/ DM[6] | — | CCL2/ IN[2]
C8 | PA25 | VDDIO | EXTINT[13] | — | — | — | — | — | — | SERCOM3/PAD[3] | SERCOM5/PAD[3] | TC1/ WO[1] | TCC1/WO[3] | USB/ DP[6] | — | CCL2/OUT[2]
E5 | PB22 | VDDIN | EXTINT[6] | — | — | — | — | — | — | — | SERCOM5/PAD[2] | TC3/ WO[0] | — | — | GCLK_IO[0] | CCL0/ IN[0]
C7 | PB23 | VDDIN | EXTINT[7] | — | — | — | — | — | — | — | SERCOM5/PAD[3] | TC3/ WO[1] | — | — | GCLK_IO[1] | CCL0/OUT[0]
E4 | PA27 | VDDIN | EXTINT[15] | — | — | — | — | — | — | — | — | — | — | — | GCLK_IO[0] | —
C6 | PA28 | VDDIN | EXTINT[8] | — | — | — | — | — | — | — | — | — | — | — | GCLK_IO[0] | —
C5 | PA30 | VDDIN | EXTINT[10] | — | — | — | — | — | — | — | SERCOM1/PAD[2] | TCC1/WO[0] | — | SWCLK | GCLK_IO[0] | CCL1/ IN[0]
D5 | PA31 | VDDIN | EXTINT[11] | — | — | — | — | — | — | — | SERCOM1/PAD[3] | TCC1/WO[1] | — | SWDIO(3) | — | CCL1/OUT[1]
B4 | PB02 | VSWOUT | EXTINT[2] | — | — | AIN[10] | — | — | — | — | SERCOM5/PAD[0] | TC2/ WO[0] | — | — | SUPC/ OUT[1] | CCL0/OUT[0]
C3 | PB03 | VSWOUT | EXTINT[3] | — | — | AIN[11] | — | — | — | — | SERCOM5/PAD[1] | TC2/ WO[1] | — | — | SUPC/VBAT | —
ATSAMR34j18B

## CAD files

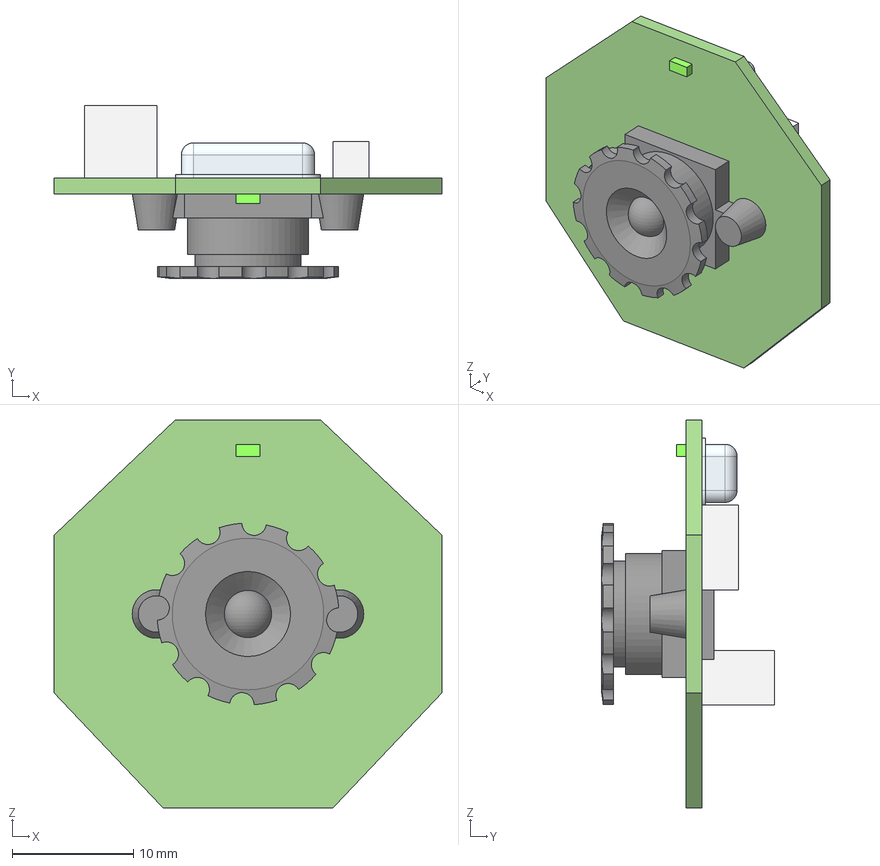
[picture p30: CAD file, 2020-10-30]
Modelados_3D/Archivos_3D/STEP/WebCam y Conector.step
32.0 x 14.3 x 32.0 mm
Camera Lens
Pins USB
Circuit Board
LED
Oscillator
Conector Audio
Conector USB
Pins Audio

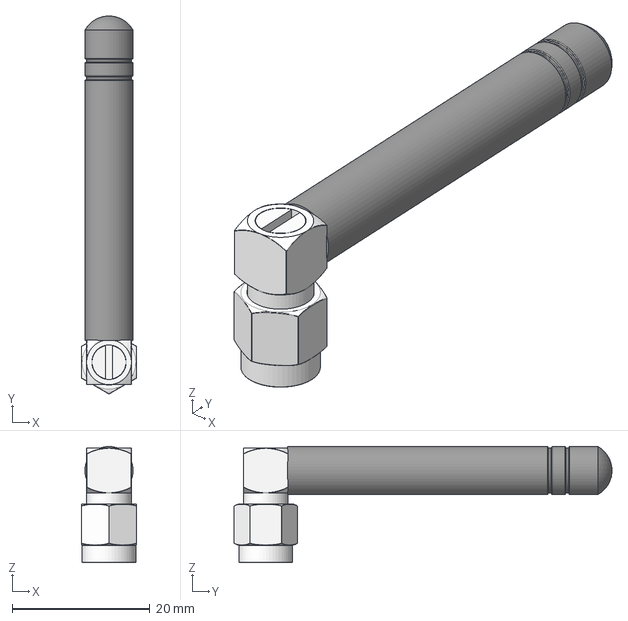
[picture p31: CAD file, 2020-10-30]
Modelados_3D/Archivos_3D/STEP/Antena - Tolina.step
8.00 x 54.9 x 16.8 mm
User Library-SMA_AntennaR x 3

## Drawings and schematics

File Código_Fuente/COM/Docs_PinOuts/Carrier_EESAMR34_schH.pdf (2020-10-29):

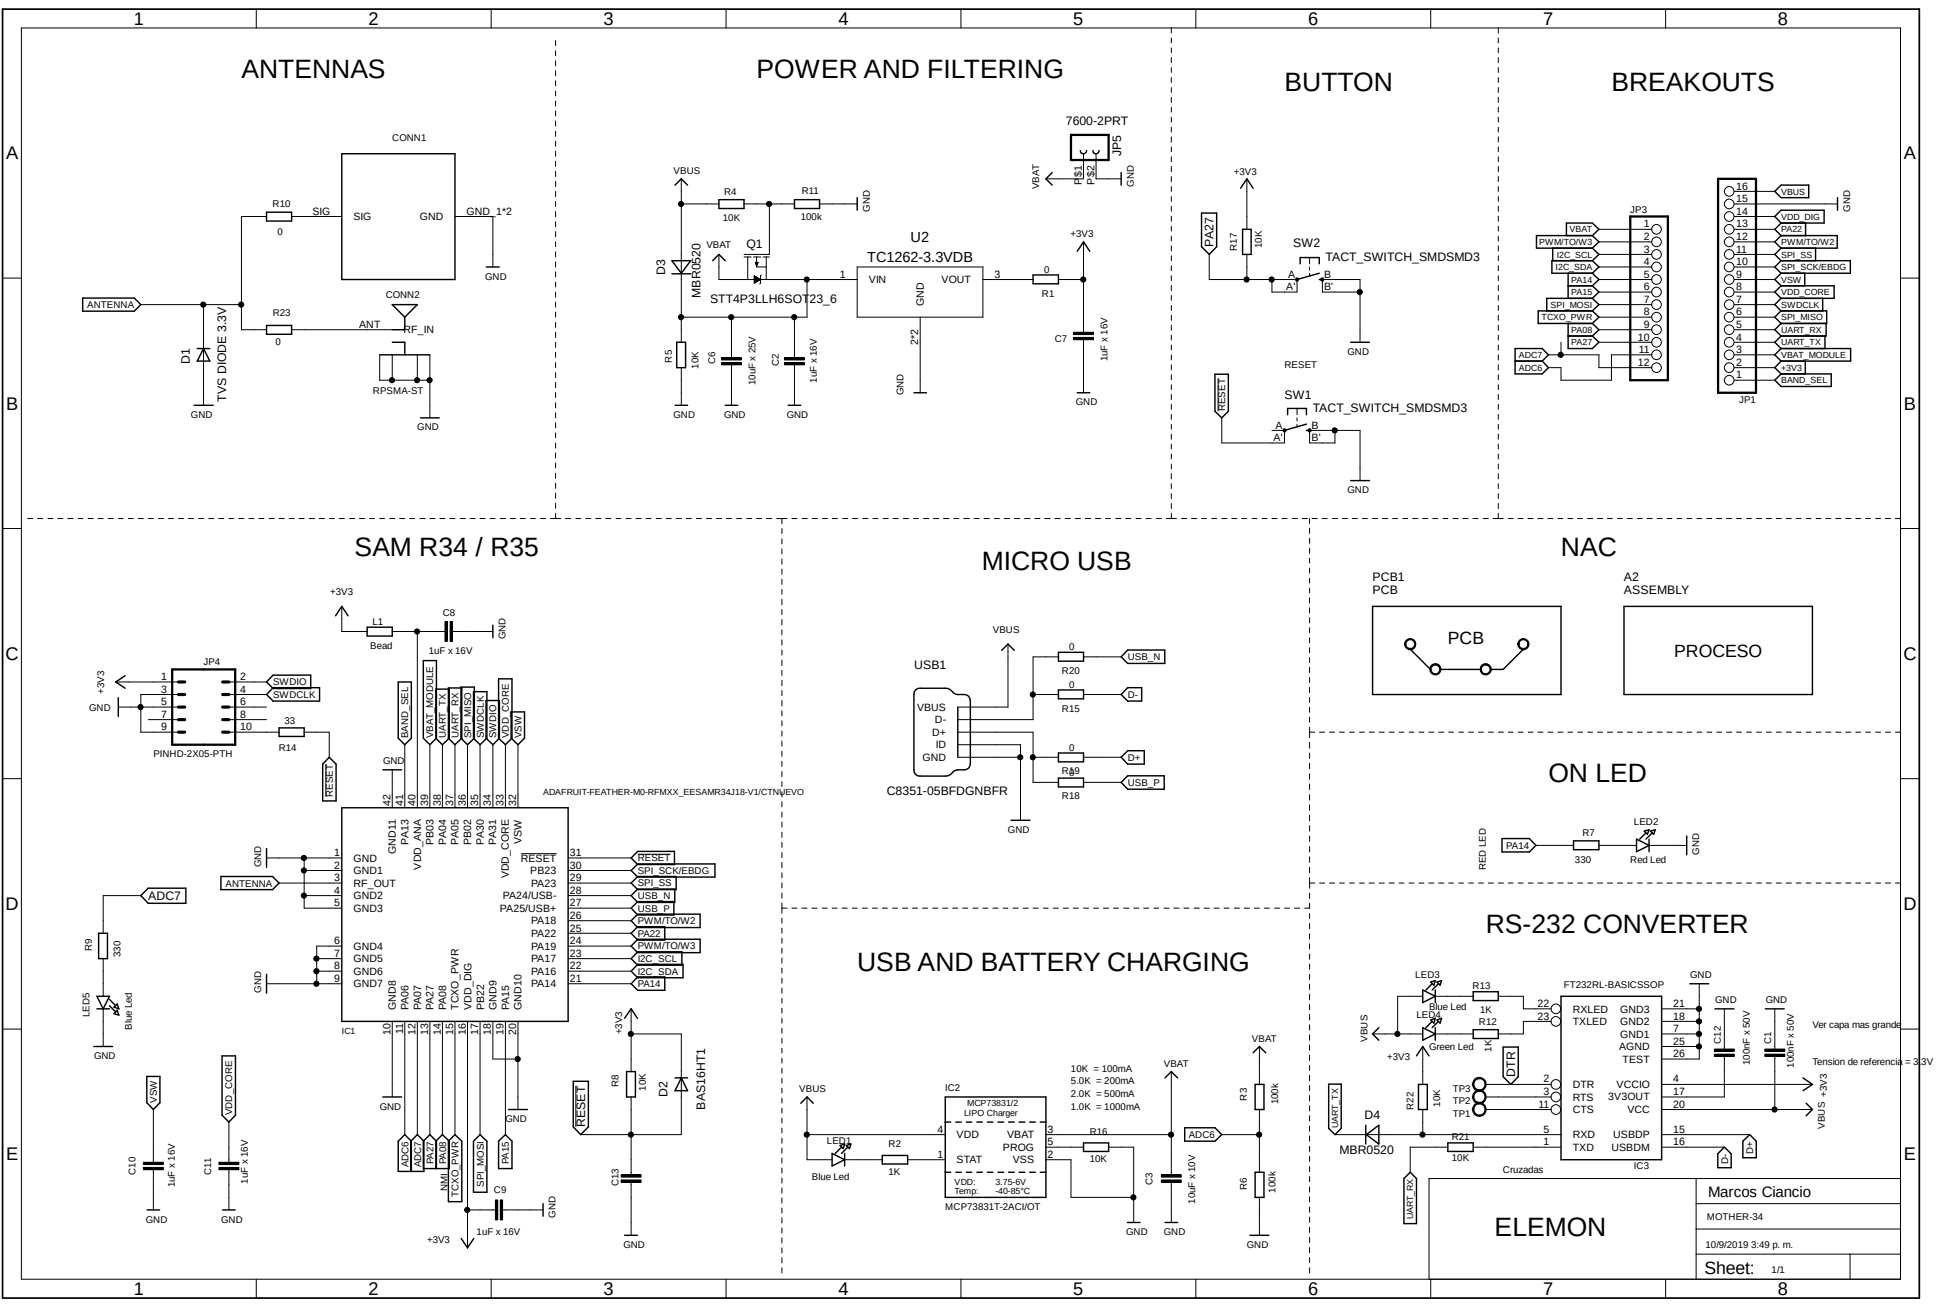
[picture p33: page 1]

RED LED ON LED RS-232 CONVERTER MICRO USB ANTENNASSAM R34 / R35 RESET BUTTON USB AND BATTERY CHARGING NAC ELEMON Marcos Ciancio Sheet: ABCDE 1 2 3 4 5 6 7 8 ABCDE 1 2 3 4 5 6 7 8 MOTHER-34 10/9/2019 3:49 p. m. 1/1 MCP73831/2 LIPO Charger Temp: -40-85°C VDD: 3.75-6V PCB PROCESO

VBAT_MODULE VBAT_MODULE POWER AND FILTERING BREAKOUTS

1uF x 16V GND 0 LED2 12345678910111213141516JP1 123456789101112 JP3 10864 1 2 3579 JP4 RF_IN ANT CONN2GND GND_1*2 SIG SIG CONN1 R7 R15 R18 R19 R20 VBUSD- D+ID GND USB1

1uF x 16V GND GND +3V3 VBUS VBAT VBAT GND GND 10K GND 100k 10K STT4P3LLH6SOT23_6 GND GND

32 IC1 ADAFRUIT-FEATHER-M0-RFMXX_EESAMR34J18-V1/CTNUEVO R1 +3V3 VBUS VBAT RESET RESET

TCXO_PWR TCXO_PWR VDD_DIG I2C_SDA I2C_SDA I2C_SCL I2C_SCL PWM/TO/W3 PWM/TO/W3 PA22 PA22 PWM/TO/W2 PWM/TO/W2 USB_P USB_P USB_N USB_N SPI_SS SPI_SS SPI_SCK/EBDG SPI_SCK/EBDG

GND GND GND GND GND PINHD-2X05-PTH GND RPSMA-STGND GND GND 330 0000 C8351-05BFDGNBFRVBUS

C13 R8 D2 VDD 4 STAT 1 VBAT 3 PROG 5 VSS 2 IC2 MCP73831T-2ACI/OT LED1 R2 C3 R16 R3 R6 3V3OUT 17 USBDM 16 USBDP 15 GND1 7 GND2 18 GND3 21 TXD 1 RXD 5 VCCIO 4 AGND 25 TEST 26 VCC 20 TXLED 23 RXLED 22 RTS 3 CTS 11 DTR 2 IC3 R12 R13 C12 C1 TP3 TP2 TP1 LED3 LED4 C8 C9 C10 C11 A B A' B' SW1

VBUS +3V3 Blue Led Green Led GND GND 1uF x 16V 1uF x 16V

100k 100k FT232RL-BASICSSOP GND GND GND

NMICruzadas Tension de referencia = 3.3V Ver capa mas grande

BAS16HT1 Blue Led 1K GND GND VBUS VBAT VBAT GND

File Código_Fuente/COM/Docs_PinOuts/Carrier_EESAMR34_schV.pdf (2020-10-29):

# TVS DIODE 3.3V GND

VBUS +3V3 | Green Led | Blue Led GND GND | 1uF x 16V 1uF x 16V

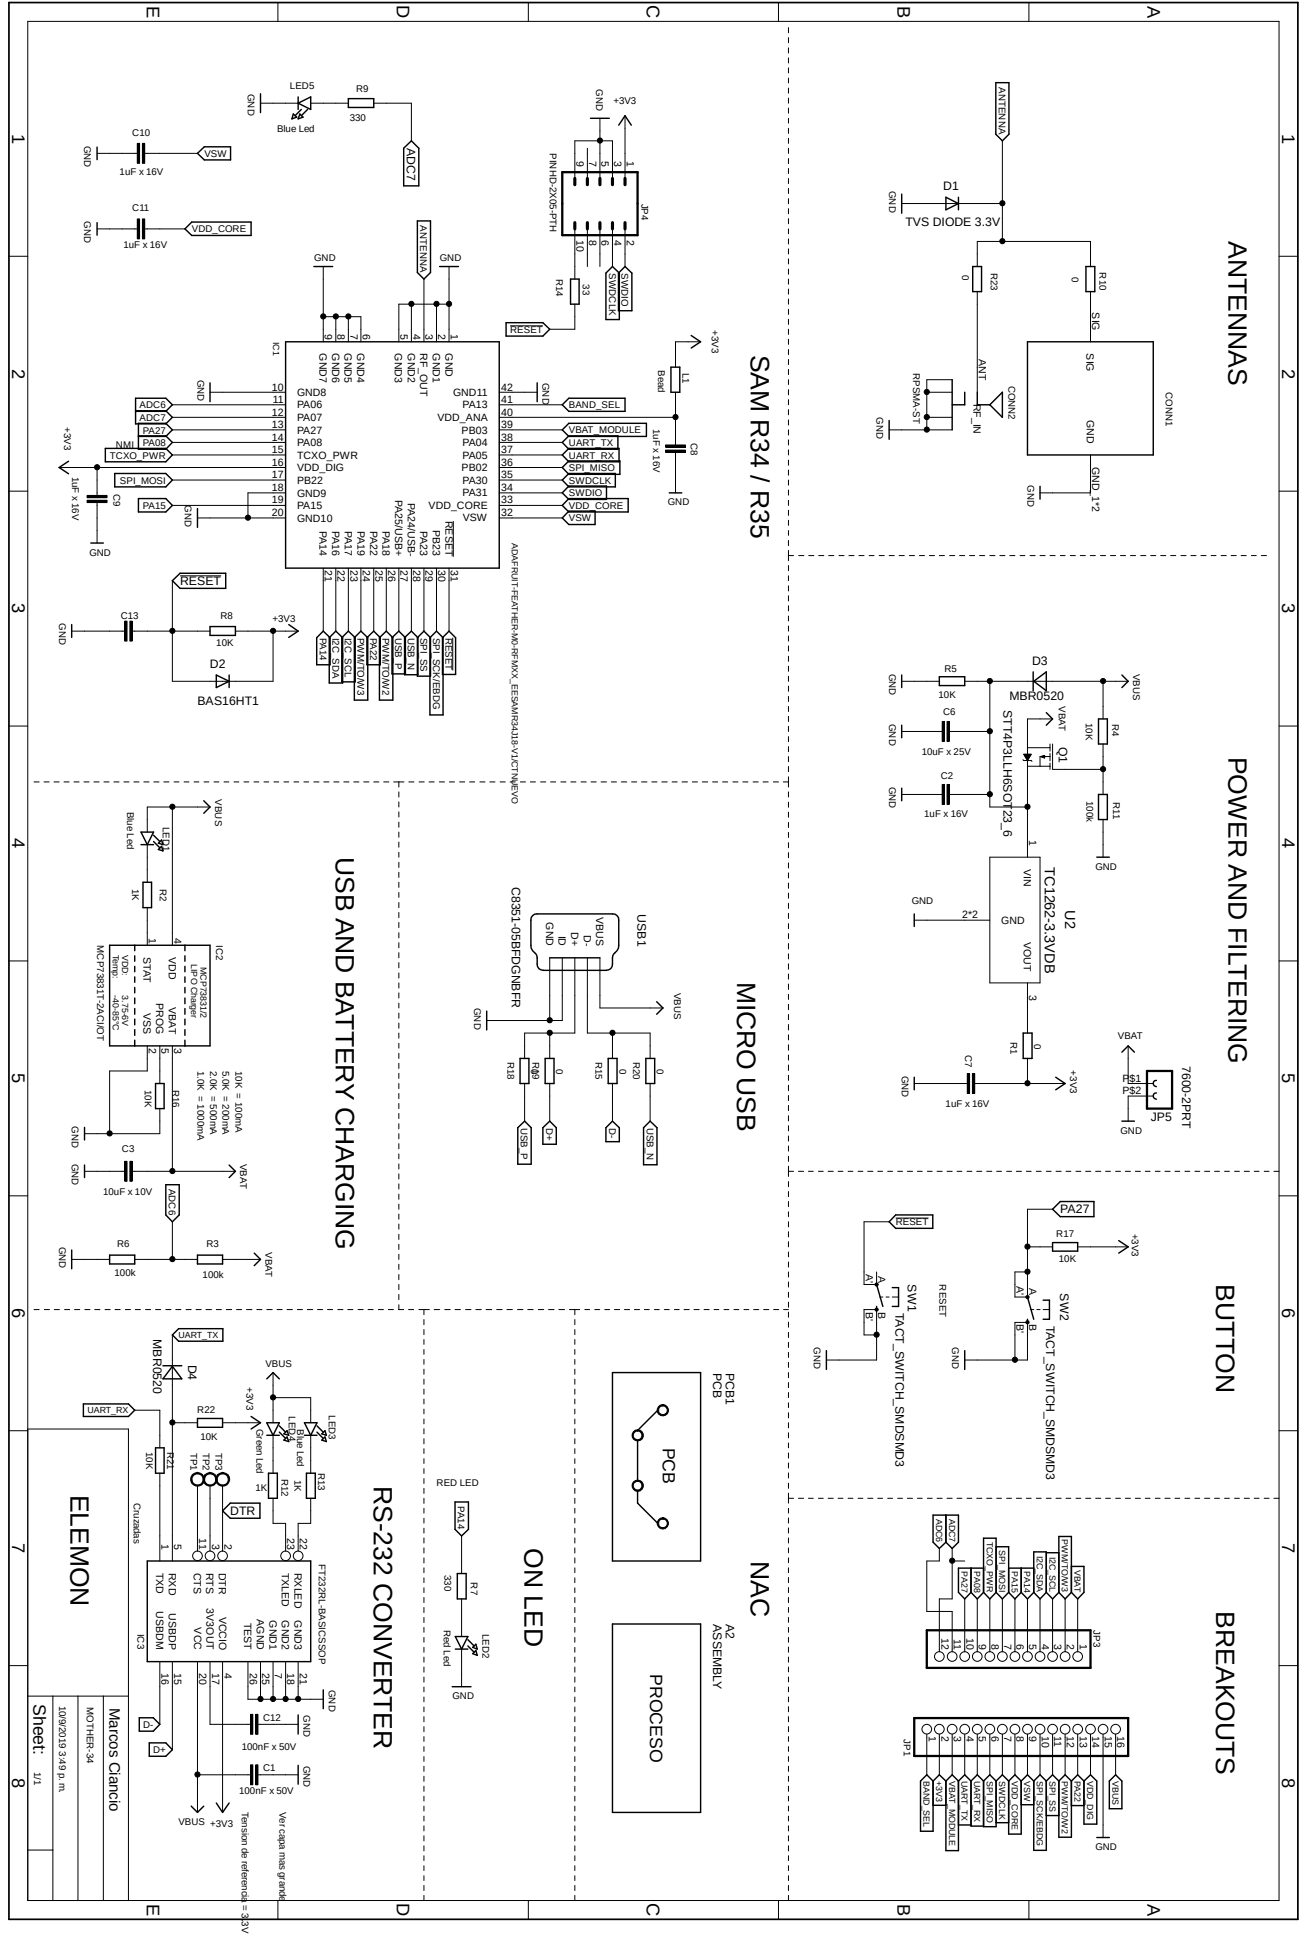
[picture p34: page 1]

1 2 3 4 5 6 7 8 10/9/2019 3:49 p. m. MOTHER-34 1/1 MCP73831/2 LIPO Charger Temp: -40-85°C VDD: 3.75-6V PCB PROCESO

1 JP4 RF_IN ANT CONN2GND GND_1*2 SIG SIG CONN1 R7 R18 R19 R15 R20 VBUSIDD+D- GND USB1

4 AGND 25 TEST 26 VCC 20 TXLED 23 RXLED 22 RTS

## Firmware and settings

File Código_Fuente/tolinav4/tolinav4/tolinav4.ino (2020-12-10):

//Initializing LED Pin
#define PWMX 2  //se usa el PWMX y PWMY PARA EL GIRO (esta decisión es concensuada) 
#define PWMY 3
#define PWMZ 4
 
#define sentidoAX1  22
#define sentidoBX1  23
#define sentidoAX2  24
#define sentidoBX2  25

#define sentidoAY1  28
#define sentidoBY1  29
#define sentidoAY2  30
#define sentidoBY2  31

#define sentidoAZ0  34
#define sentidoBZ0  35

//pote 1 x,y  | pote2 z,w
#define Xmin 0        //271  //ok
#define Xmed 512      // 527
#define Xumbral 50        //real 25
#define Xmax 999 //ok 

#define Ymin 0
#define Ymed 512  //386
#define Yumbral 50  //real 126
#define Ymax 999 //ok

#define Zmin 0 // 312
#define Zmed 512 //480
#define Zumbral 50 //70 //real 50
#define Zmax 999  //796

#define Wmin 0
#define Wmed 512   // 646
#define Wumbral 50  //220 //real 209
#define Wmax 999 //1024

boolean Xon = false;  
boolean Yon = false; 
boolean Zon = false; 
boolean Won = false; //chequeo por motores compartidos

void setup() {

  pinMode(PWMX, OUTPUT);
  pinMode(PWMY, OUTPUT);
  pinMode(PWMZ, OUTPUT);
  
  pinMode(sentidoAX1,OUTPUT);
  pinMode(sentidoBX1,OUTPUT);
  pinMode(sentidoAX2,OUTPUT);
  pinMode(sentidoBX2,OUTPUT);
  
  pinMode(sentidoAY1,OUTPUT);
  pinMode(sentidoBY1,OUTPUT);
  pinMode(sentidoAY2,OUTPUT);
  pinMode(sentidoBY2,OUTPUT);
  
  pinMode(sentidoAZ0,OUTPUT);
  pinMode(sentidoBZ0,OUTPUT);
  
  Serial.begin(9600);
}

void tipodemaniobra(int X,int Y,int Z,int W){ //eje: x=1; y=2; z=3, giro = 4 sentido          1=adelante/horario ; -1=atras/antihorario ;
//configuro el sentido de rotacion de los motores segun el eje y sentido
boolean entroxoy = false;
int Xmap,Ymap,Zmap,Wmap;

  //mapeo de valores
  if(X>Xmed+Xumbral){  //x+
    
      Xmap = round(((X-(Xmed+Xumbral))/(float)(Xmax-(Xmed+Xumbral)))*215);   
      Serial.print("Xmap+ = ");
      Serial.println(Xmap);
      digitalWrite(sentidoAX1, HIGH); 
      digitalWrite(sentidoBX1, LOW);
      digitalWrite(sentidoAX2, HIGH); 
      digitalWrite(sentidoBX2, LOW);
      Xon = true;
      
  }else if(X<Xmed-Xumbral){  // X-
      
      Xmap = round(((X-(Xmed-Xumbral))/(float)(Xmin-(Xmed-Xumbral)))*215); 
      Serial.print("Xmap- = ");
      Serial.println(Xmap);
      digitalWrite(sentidoAX1, LOW);
      digitalWrite(sentidoBX1, HIGH);
      digitalWrite(sentidoAX2, LOW); 
      digitalWrite(sentidoBX2, HIGH);
      Xon = true;
      
  }else{   // no va: if(X<(Xmed+Xumbral) || X>(Xmed-Xumbral)){  //si x se encuentra cercano al cero
      Xon = false;
      if(Won == false) analogWrite(PWMX, 0); //Won es global, por tanto queda del loop anterior
      Xmap = 0; //para test
  }

  if(Xon){

    if(Xmap > 215) Xmap = 215;  
    if(Xmap <= 0) Xmap = 0;  
    analogWrite(PWMX, Xmap + 40);  
  }

  if(Y>Ymed+Yumbral){  //Y+
    
      Ymap = round(((Y-(Ymed+Yumbral))/(float)(Ymax-(Ymed+Yumbral)))*215);  
      Serial.print("Ymap+ = ");
      Serial.println(Ymap);
      digitalWrite(sentidoAY1, HIGH); 
      digitalWrite(sentidoBY1, LOW);
      digitalWrite(sentidoAY2, HIGH); 
      digitalWrite(sentidoBY2, LOW);
      Yon = true;
      
  }else if(Y<Ymed-Yumbral){  // X-

      Ymap = round(((Y-(Ymed-Yumbral))/(float)(Ymin-(Ymed-Yumbral)))*215); 
      Serial.print("Ymap- = ");
      Serial.println(Ymap);
      digitalWrite(sentidoAY1, LOW);
      digitalWrite(sentidoBY1, HIGH);
      digitalWrite(sentidoAY2, LOW); 
      digitalWrite(sentidoBY2, HIGH);
      Yon = true;

  }else{  //si Y se encuentra cercano al cero
      Yon = false;
      if(Won == false) analogWrite(PWMY, 0);
      Ymap = 0; 
  }

  if(Yon){

    if(Ymap > 215) Ymap = 215; 
    if(Ymap <= 0) Ymap = 0;  
    analogWrite(PWMY, Ymap + 40);  
  }

  if(Z>Zmed+Zumbral){  //Z+
    
      Zmap = round(((Z-(Zmed+Zumbral))/(float)(Zmax-(Zmed+Zumbral)))*215);  
      Serial.print("Zmap+ = ");
      Serial.println(Zmap);
      digitalWrite(sentidoAZ0, HIGH);
      digitalWrite(sentidoBZ0, LOW);
      Zon = true;
 
  }else if(Z<Zmed-Zumbral){  // Z-
      
      Zmap = round(((Z-(Zmed-Zumbral))/(float)(Zmin-(Zmed-Zumbral)))*215); 
      Serial.print("Zmap- = ");
      Serial.println(Zmap);
      digitalWrite(sentidoAZ0, LOW);
      digitalWrite(sentidoBZ0, HIGH);
      Zon = true;
      
  }else{  //si z se encuentra cercano al cero
    
      Zon = false;
      analogWrite(PWMZ, 0);
  }

  if(Zon){

    if(Zmap > 215) Zmap = 215; 
    if(Zmap <= 0) Zmap = 0;  
    analogWrite(PWMZ, Zmap + 40);  
  }

  if(!(Xon && Yon)){ //W - si alguna de las dos tralsaciones está apagada (sino no hay rotacion)
    
    if(W>Wmed+Wumbral){  //W+ giro horario
       
        Wmap = round(((W-(Wmed+Wumbral))/(float)(Wmax-(Wmed+Wumbral)))*215);  
        Serial.print("Wmap+ = ");
        Serial.println(Wmap);
        if(Xon == false){ //si no estoy usando X entonces configuro para girar horario
          digitalWrite(sentidoAX1, HIGH);
          digitalWrite(sentidoBX1, LOW);
          digitalWrite(sentidoAX2, LOW); 
          digitalWrite(sentidoBX2, HIGH);
        }
        if(Yon == false){ //si no estoy usando Y entonces configuro para girar horario
          digitalWrite(sentidoAY1, HIGH);
          digitalWrite(sentidoBY1, LOW);
          digitalWrite(sentidoAY2, LOW); 
          digitalWrite(sentidoBY2, HIGH);
        }
        Won = true;
        
    }else if(W<Wmed-Wumbral){  // X-
        
        Wmap = round(((W-(Wmed-Wumbral))/(float)(Wmin-(Wmed-Wumbral)))*215); 
        Serial.print("Wmap- = ");
        Serial.println(Wmap);

        if(Xon == false){   //si no estoy usando X entonces configuro para girar antihorario
          digitalWrite(sentidoAX1, LOW);
          digitalWrite(sentidoBX1, HIGH);
          digitalWrite(sentidoAX2, HIGH); 
          digitalWrite(sentidoBX2, LOW);
        }
        if(Yon == false){ //si no estoy usando Y entonces configuro para girar antihorario
          digitalWrite(sentidoAY1, LOW);
          digitalWrite(sentidoBY1, HIGH);
          digitalWrite(sentidoAY2, HIGH); 
          digitalWrite(sentidoBY2, LOW);
        }
  
        Won = true;
        
    }else{   //si W se encuentra cercano al cero
        
        Won = false;
        if(Xon == false) analogWrite(PWMX, 0); //Won es global, por tanto queda del loop anterior
        if(Yon == false) analogWrite(PWMY, 0);
        Xmap = 0; //para test
    }
  
    if(Won){
    
        if(Wmap > 215) Wmap = 215; 
        if(Wmap <= 0) Wmap = 0;  
        if(Xon == false) analogWrite(PWMX, Wmap + 40); //si no se activa queda el de la tralsacion 
        if(Yon == false) analogWrite(PWMY, Wmap + 40); // ""  idem
     }
    
  }else{
    Serial.println("no entró a W"); //para test
  }

}

void loop(){ //eje: x=1; y=2; z=3, giro = 4 sentido; 1=adelante/horario ; -1=atras/antihorario ; visto desde techo de carpa 

  //CONVERSION DE TEXTO A VARIABLES DE CONTROL
  boolean msjok = true;
  boolean barra = false;
  char payload[14];// = "000000000000/"; // = "527100320900/"; //"123456789666/";
  int i = 0; 

  
  /*while(Serial.available()>0 && barra == false){
    
    payload[i] = Serial.read();
    if(payload[i] == '/') barra = true;
      //Serial.println(Serial.read() - '0');
      i++;
    //Serial.println("entra a Serial.available"); 
  }
  Serial.print("contador i llego hasta:  ");
  Serial.println(i);
  Serial.println(payload);*/
  
  while(Serial.available() > 0){
    Serial.readBytesUntil('\n',payload,13);
    /*i++;
    if(payload[i-1] == '\n'){
      payload[i-i] = 0;
      i = 0;
      Serial.println(payload);
    }*/
    Serial.println(payload);
  }
  delay(2000);
  
  
    for(int i = 0;i <= 11;i++){
      if(!isDigit(payload[i])){
        Serial.print("Error, no es numérico = "); //funciona la validacion
        Serial.println(payload[i]);
        msjok = false;
      }
    }
    if(payload[12] != '/'){
      Serial.println("Error de fin de comando = "); 
      msjok = false;
    }

    if(msjok){
     
      int X = (payload[0]- '0')*100 + (payload[1]- '0')*10 + (payload[2]- '0')*1;
      int Y = (payload[3]- '0')*100 + (payload[4]- '0')*10 + (payload[5]- '0')*1;
      int Z = (payload[6]- '0')*100 + (payload[7]- '0')*10 + (payload[8]- '0')*1;
      int W = (payload[9]- '0')*100 + (payload[10]- '0')*10 + (payload[11]- '0')*1;
      Serial.println("Separacion de char a int"); 
      Serial.println(X);
      Serial.println(Y);
      Serial.println(Z);
      Serial.println(W);
  
      tipodemaniobra(X,Y,Z,W);
    }
    //delay(5000); //solo para poder ver el monitor
}

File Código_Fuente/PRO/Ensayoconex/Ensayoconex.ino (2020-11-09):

//Initializing LED Pin
#define PWMX 2  //se usa el PWMX PARA EL GIRO (esta decisión es arbitraria) 
#define PWMY 3
#define PWMZ 4
#define PWMW 5 
#define sentidoAX1  22
#define sentidoBX1  23
#define sentidoAX2  24
#define sentidoBX2  25

#define sentidoAY1  28
#define sentidoBY1  29
#define sentidoAY2  30
#define sentidoBY2  31

#define sentidoAZ0  34
#define sentidoBZ0  35

int dutycycle = 255; //despues vamos a poner un dutycylce por cada pwm, asi se puede hacer multi pwm's

void setup() {

  pinMode(PWMX, OUTPUT);
  pinMode(PWMY, OUTPUT);
  pinMode(PWMZ, OUTPUT);
  pinMode(PWMW, OUTPUT);
  pinMode(sentidoAX1,OUTPUT);
  pinMode(sentidoBX1,OUTPUT);
  pinMode(sentidoAX2,OUTPUT);
  pinMode(sentidoBX2,OUTPUT);
  
  pinMode(sentidoAY1,OUTPUT);
  pinMode(sentidoBY1,OUTPUT);
  pinMode(sentidoAY2,OUTPUT);
  pinMode(sentidoBY2,OUTPUT);
  
  pinMode(sentidoAZ0,OUTPUT);
  pinMode(sentidoBZ0,OUTPUT);
  
  Serial.begin(9600);
}

void tipodemaniobra(int eje,int sentido,int dutycycle){ //eje: x=1; y=2; z=3, giro = 4 sentido          1=adelante/horario ; -1=atras/antihorario ;
//configuro el sentido de rotacion de los motores segun el eje y sentido
  switch(eje){
    case 1:{ //eje x
          if(sentido == 1){  
            digitalWrite(sentidoAX1, HIGH);
            digitalWrite(sentidoBX1, LOW);
            digitalWrite(sentidoAX2, HIGH); 
            digitalWrite(sentidoBX2, LOW);
          }else if(sentido == -1){
            digitalWrite(sentidoAX1, LOW);
            digitalWrite(sentidoBX1, HIGH);
            digitalWrite(sentidoAX2, LOW); 
            digitalWrite(sentidoBX2, HIGH);
          }
          analogWrite(PWMX, dutycycle);
    }break;
    case 2:{ //eje y
          if(sentido == 1){
            digitalWrite(sentidoAY1, HIGH);
            digitalWrite(sentidoBY1, LOW);
            digitalWrite(sentidoAY2, HIGH); 
            digitalWrite(sentidoBY2, LOW);
          }else if(sentido == -1){
            digitalWrite(sentidoAY1, LOW);
            digitalWrite(sentidoBY1, HIGH);
            digitalWrite(sentidoAY2, LOW); 
            digitalWrite(sentidoBY2, HIGH);
          }
          analogWrite(PWMY, dutycycle);
      
    }break;
    case 3:{  //eje z
          if(sentido == 1){
            digitalWrite(sentidoAZ0, HIGH);
            digitalWrite(sentidoBZ0, LOW);
            
          }else if(sentido == -1){
            digitalWrite(sentidoAZ0, LOW);
            digitalWrite(sentidoBZ0, HIGH);
          }
          analogWrite(PWMZ, dutycycle);
    }break;

    case 4:{  //giro
          if(sentido == 1){  //horario
            digitalWrite(sentidoAX1, HIGH);
            digitalWrite(sentidoBX1, LOW);
            digitalWrite(sentidoAX2, LOW); 
            digitalWrite(sentidoBX2, HIGH);
            digitalWrite(sentidoAY1, HIGH);
            digitalWrite(sentidoBY1, LOW);
            digitalWrite(sentidoAY2, LOW); 
            digitalWrite(sentidoBY2, HIGH);
          }else if(sentido == -1){      
            digitalWrite(sentidoAX1, LOW);
            digitalWrite(sentidoBX1, HIGH);
            digitalWrite(sentidoAX2, HIGH); 
            digitalWrite(sentidoBX2, LOW);
            digitalWrite(sentidoAY1, LOW);
            digitalWrite(sentidoBY1, HIGH);
            digitalWrite(sentidoAY2, HIGH); 
            digitalWrite(sentidoBY2, LOW);
          }  
          analogWrite(PWMX, dutycycle);
          analogWrite(PWMY, dutycycle);
    }break;
    default:{
      Serial.print("no se reconoce el comando"); 
    }
  }

}

void loop() { //eje: x=1; y=2; z=3, giro = 4 sentido; 1=adelante/horario ; -1=atras/antihorario ; visto desde techo de carpa 

  //aca los imputs serian que maniobra hacer , con que dutycycle el pwm

  //ensayo de maniobras una por una con 6 segundos de delay
  Serial.println("+X por 300 segundos");
  tipodemaniobra(1,1,dutycycle);
  delay(30000);
  analogWrite(PWMX, 0);
  delay(1000);
  

  Serial.println("+Y");
  tipodemaniobra(2,1, dutycycle);
  delay(30000);
  analogWrite(PWMY, 0);
  delay(1000);


  Serial.println("+Z");
  tipodemaniobra(3,1, dutycycle);
  analogWrite(PWMZ, dutycycle);
  delay(30000);
  analogWrite(PWMZ, 0);
  delay(1000);


}

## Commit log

2020-10-12 primeros commits, estudiando el funionamiento de github
2020-10-12 algunas mejoras y ensayos de commits
2020-10-12 mejora de reques
2020-10-12 codigos de ejemplo de WiringPi
2020-10-13 mejora de requerimientos e imagenes
2020-10-23 Primer codigo de Marian
2020-10-23 reordenamiento de carpetas de codigo
2020-10-23 agregado HeatSink a 3D
2020-10-26 Create SAMR34_GettingStarted_LoRaWAN Range Test [Button] QuickStart_Guide_v1.0.pdf
    Documentos de LoRaWAN Atmel Studio
2020-10-26 SAMR34 ASF3
    Documentos de estudio - Vic
2020-10-27 Primer Commit de LoRa
    Primer version funcional de Codigo fuente del subsistema de comunicaciones. El boton enciende el LED y muestra en pantalla la lectura del pina ADC aun no identificado, tambien busca conectarse OTAA p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
2020-10-28 segundo commit de COM, esta vez hace lo que tiene que hacer, resta fucionarlo con el anterior
    [ATSAMR34_LORA_P2P_SIMPLE_APP.componentinfo.xml]
2020-10-28 Planilla SAMR34
    [SAMR34J18B.xlsx]
2020-10-28 Info pinout SAMR34
    Sobre el micro y lo disponible en el kit de Elemon
    [SAMR34J18B.xlsx]
2020-10-28 Leame de código fuente
2020-10-28 Leame de código fuente. adds
2020-10-29 Create Joystick2.ino
    Borrador del codigo para Joystick
2020-10-29 agregado de codigos de Marian
2020-10-29 Joystick1
    Subi el programa completo del joystick, llamado joystick1 y sus librerias en una carpeta aparte.
2020-10-29 reordenado de codigos de Marian
2020-10-29 ayudin para Marian
2020-10-30 nuevo 3D
    [Antena - Tolina.step]
2020-10-30 nuevo 3D webcam
    [WebCam y Conector.step]
2020-10-30 texto de readme
2020-10-30 codio para marian
2020-11-03 codigo para marian
    [Antena - Tolina.step, WebCam y Conector.step]
2020-11-04 Codigo Serial USB TTL
    [SAMR34J18B.xlsx]
2020-11-07 PCB de Shield OBC
2020-11-08 Hardware
    Archivos para la impresion a hoja de PCB experimental
2020-11-16 Código de Joystick, Trama implementada, Filto implementado. Verificado por emulador disponible en https://www.tinkercad.com/things/3AbcvOwmZ8W
2020-11-16 imagen Shield Arduino onshape
2020-11-16 archivos de propulsion
    Aca están todo los soft de propulsion
    el programa tolinav3
    y por otra parte el programa Shield_l293 + su librería.
2020-11-18 virtualizacion y estudio de Shield sin librerias
2020-12-05 Carpeta de Proyecto
2020-12-11 Ultima version de codigo de Joystick, agregado cambio de salto de linea por barra diagonal en trama de datos ascendente
    [ATSAMR34_LORA_P2P_SIMPLE_APP.componentinfo.xml, Antena - Tolina.step, SAMR34J18B.xlsx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]
2020-12-16 Documentacion de proyecto final
2020-12-16 Presentación de proyecto Critical Design Review
2020-12-16 mas imagenes de 3D
2020-12-16 PCB interconexion imagen real
2020-12-18 Power Bank 3D agregado
2020-12-18 onshape de PCD de dedicado
